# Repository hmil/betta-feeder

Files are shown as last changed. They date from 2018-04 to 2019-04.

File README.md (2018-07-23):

DIY IoT Feeder for my Betta Fish
================================

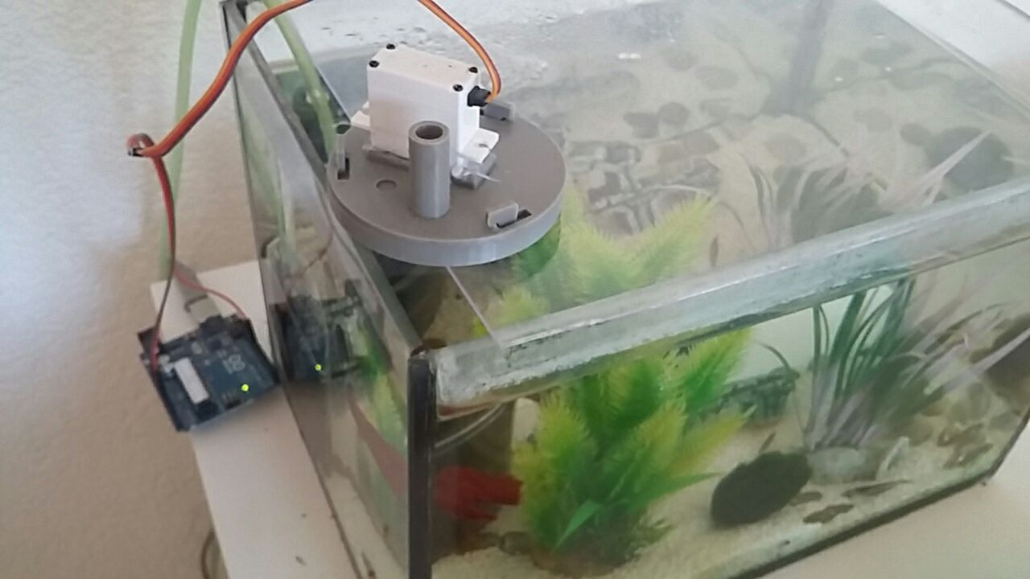
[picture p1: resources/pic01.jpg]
Feeder picture

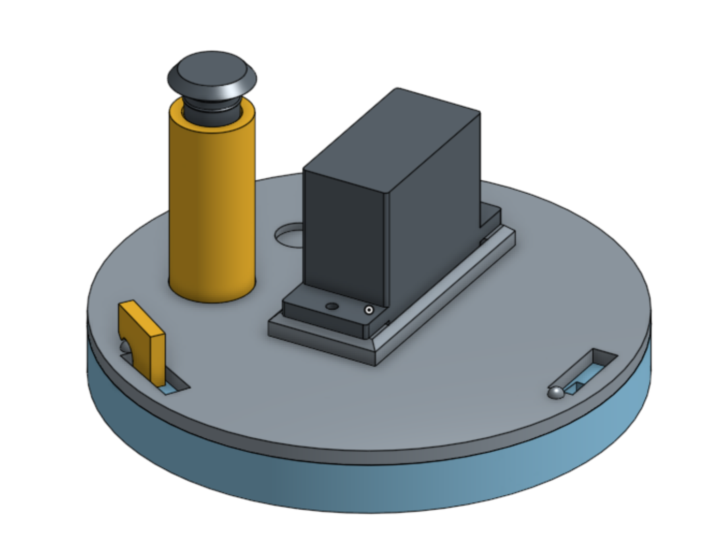
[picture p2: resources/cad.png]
CAD model rendering

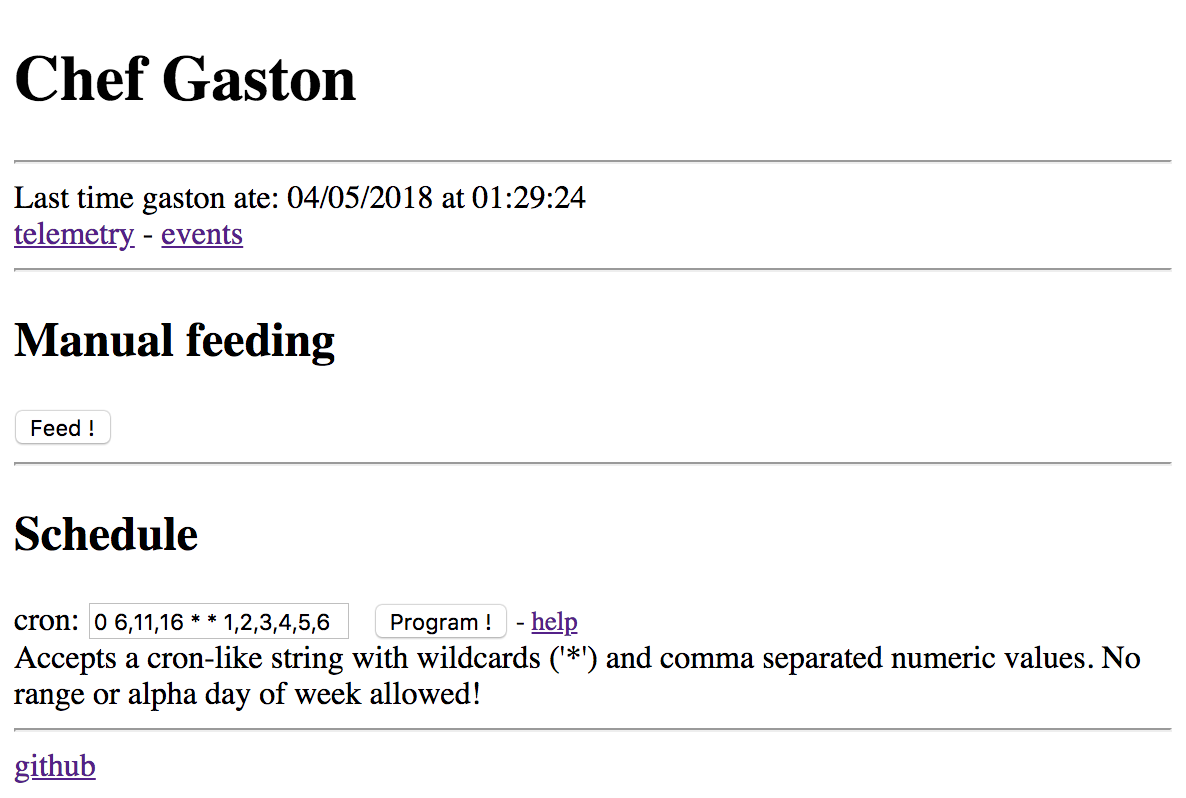
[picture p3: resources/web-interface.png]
web control interface


## Features

- precise quantities, food is delivered in predefined increments
- Large autonomy: The system works as long as there is food left in the reservoir.
- Robust design with only one moving part.

## What you need

- An arduino board OR a NodeMCU / ESP-12 or any esp8266-based board supported by NodeMCU
- A servomotor
- An AC adapter for the arduino / MCU
- A 3d printer

## Setup

Print and assemble all parts according to the cad model. Make sure to leverage the base plate of your printer to get smooth surfaces for the inside of the case and the base of the rotor (this will prevent food from getting caught between the rotor and the case).
Mount the servomotor on top and connect it to the arduino's VCC (red wire), Gnd (black wire) and pin 9 (remaining wire). I found that the capacitors on the board are sufficient to operate the servo without loss of power. If you do lose power when the servo moves, connect the servo's red and black wire through a breadboard and put one or two capacitors of more than 100uF in between.

## How it works

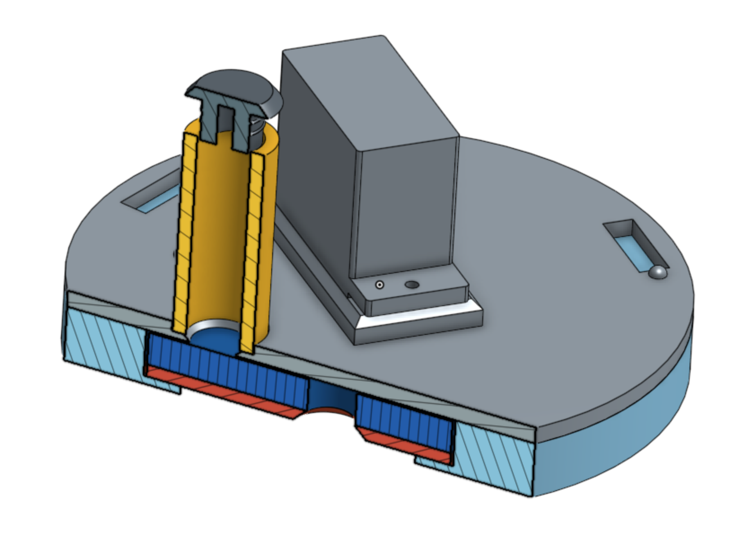
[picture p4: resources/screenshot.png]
Cut view


A hole on a rotating disk alternatively aligns with a food reservoir on top and a dispensing hole at the bottom. The disk is actionned by a servomotor at scheduled times.

## Hardware

The CAD is [hosted at onshape](https://cad.onshape.com/documents/9ce24f0eb68b5dfcb29f30d2). You will probably need to modify it so that it fits your specific servo.

Be sure to print the surfaces that will be in contact with the rotor facing the bottom. This way you'll get the smoothest possible surfaces and prevent food from getting stuck into the mechanism.

Ready-to-print STL files are available under `hardware/`. Tested on a prusa i3 mk2; It took a little bit of grinding to get them all to fit together.

## Software

### Arduino

There is an arduino sketch providing basic functionality. It is a prototype and has major flaws:
- Programming the schedule requires to change the software code and flash the arduino with the new program.
- The schedule is relative to the boot time of the arduino. In the event of an AC outage, there is a risk for feeding too much or too little.

### NodeMCU

A NodeMCU project is available as well. It is safer and has more features than the arduino code, but is a little more complex to use.

Connect the servomotor to GPIO 12. Be careful that the board runs at 3.3v whereas a servo usually runs at 5v (You don't need a logic converter for the control signal... just beware not to connect the board's 3.3v to the servo's VCC). Make a copy of the `.example` files without the `.example` extension and replace the variables according to your environment.

The NodeMCU software must be configured to talk to an MQTT broker. A companion server (located in `/server`) provides a user interface and connects to the same broker to collect data and send commands to the device. Run the server with Node.JS and the proper environment variables (MQTT_HOST, MQTT_PORT, MQTT_USER, MQTT_PASSWORD).

The server lets you manually trigger the feeder and allows you to program the schedule using a cron-like syntax. It also lets you see historical data of the device.

Contrary to the Arduino sketch, the NodeMCU solution is more reliable as it uses NTP to keep track of wall clock time. There is no risk of over-delivery and little risk of missed deliveries.

## Known issues

- There is not enough play between the rotor and the carter and it requires quite a bit of grinding to get it to slide well.
- The top part is designed based on an unusual servomotor format. (I got a larger servo to fit using hot glue though).
- The reservoir is too narrow and is a real pain to refill.

**If you fix any of these issues, make sure to contribute your changes back!**

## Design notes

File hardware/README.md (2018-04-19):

This folder contains STL files exported from [this onshape project](https://cad.onshape.com/documents/9ce24f0eb68b5dfcb29f30d2).

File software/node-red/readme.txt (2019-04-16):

This is a companion application which talks to the nodemcu-based software over MQTT.

It is implemented with node-red.

Deploy a node-red instance and import flow.json into it. You'll need to configure the paths of 
the file storage and the sqlite database, as well as the credentials to connect to your MQTT server.

The flow uses the following modules:
- https://flows.nodered.org/node/node-red-dashboard
- https://flows.nodered.org/node/node-red-node-sqlite

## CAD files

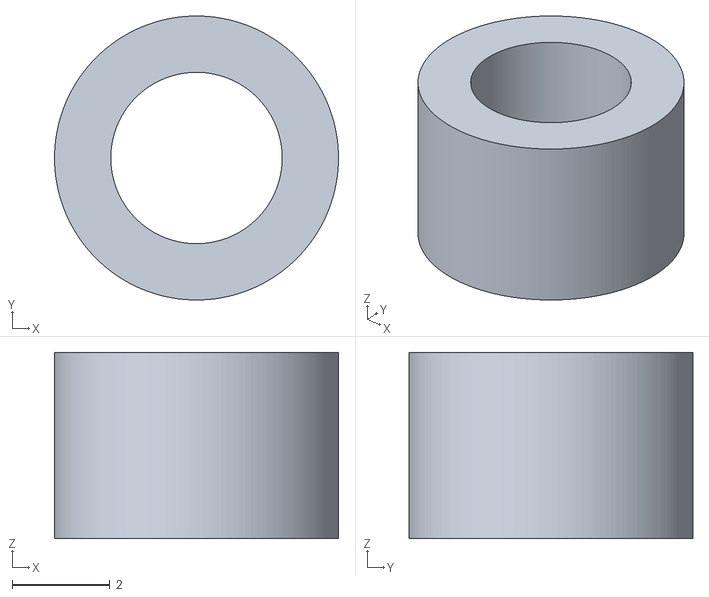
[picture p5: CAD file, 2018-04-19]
hardware/reducer insert 2.stl
5.80 x 5.80 x 3.80

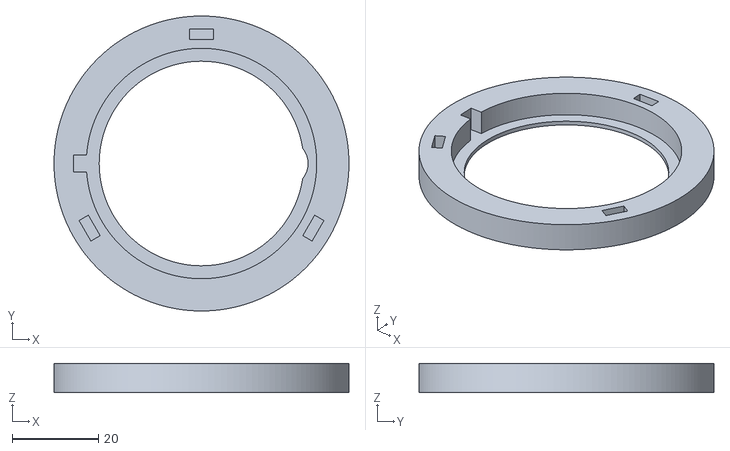
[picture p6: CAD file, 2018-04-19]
hardware/carter.stl
68.5 x 68.5 x 6.75

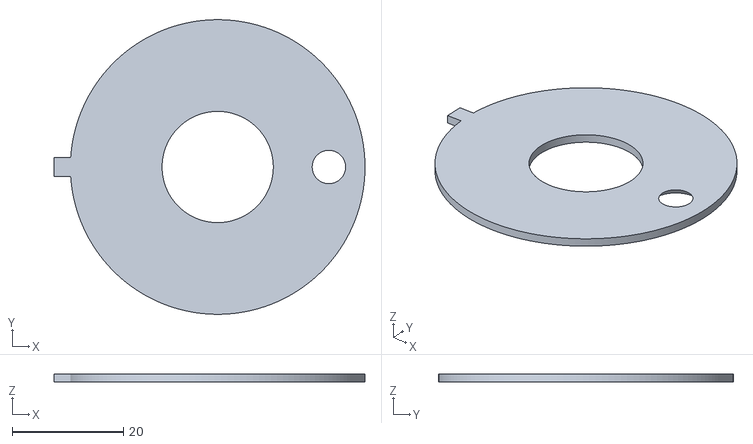
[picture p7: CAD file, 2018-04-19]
hardware/base plate.stl
55.9 x 53.0 x 1.50

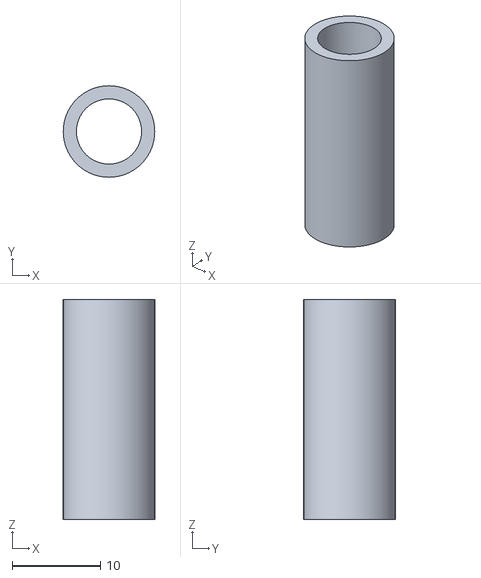
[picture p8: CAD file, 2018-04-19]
hardware/reservoir.stl
10.4 x 10.4 x 25.0

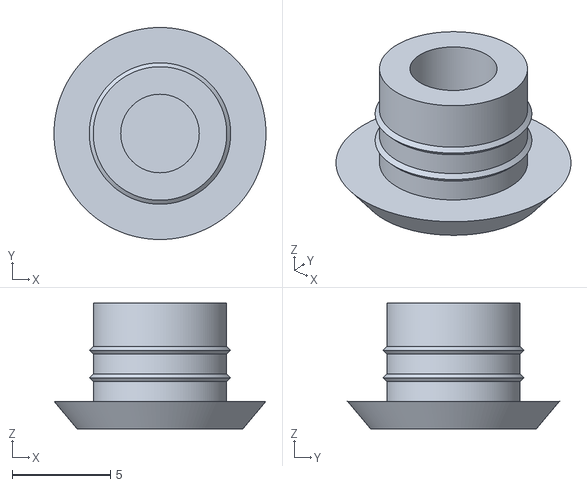
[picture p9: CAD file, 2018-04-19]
hardware/reservoir cap.stl
10.8 x 10.8 x 6.40

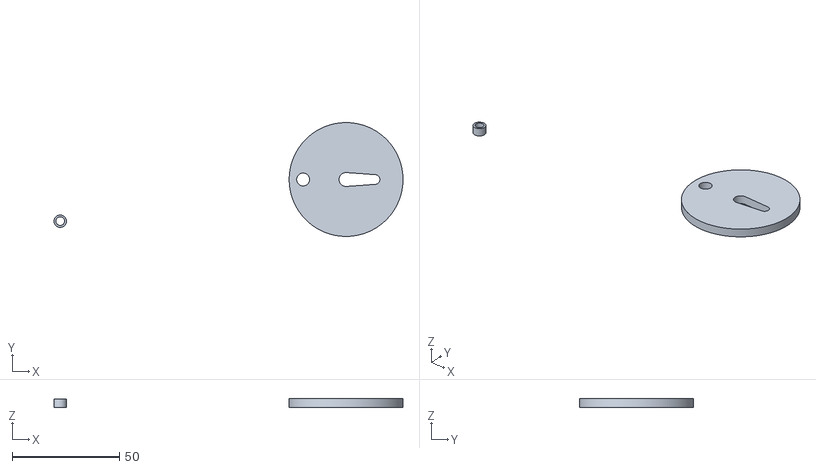
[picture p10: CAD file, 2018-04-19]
hardware/reducer insert 1.stl
162.5 x 53.0 x 4.00

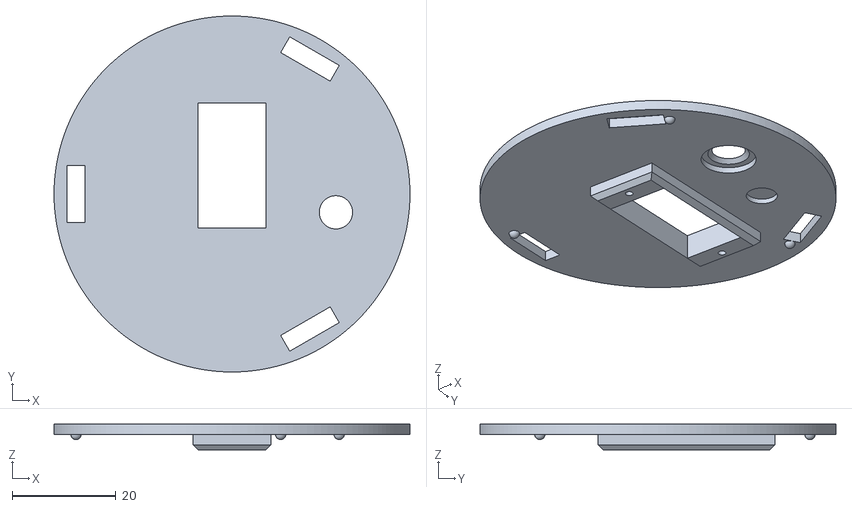
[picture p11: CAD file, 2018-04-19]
hardware/top.stl
68.5 x 68.5 x 5.00

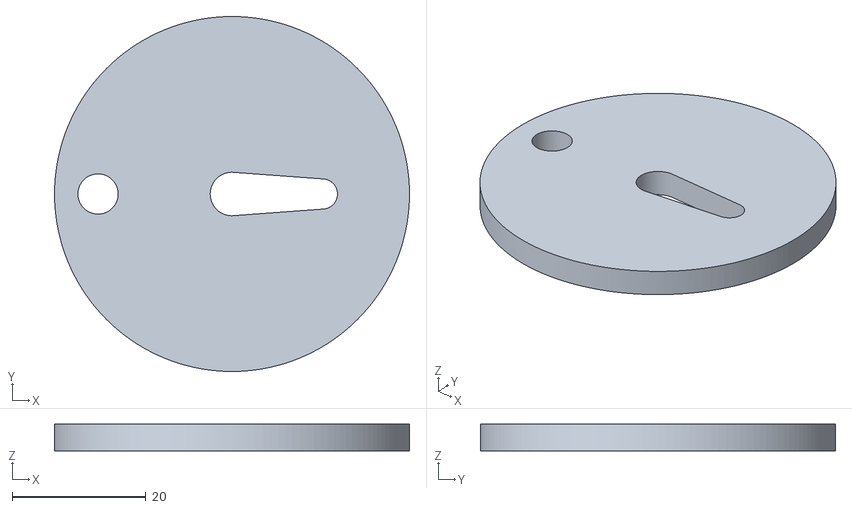
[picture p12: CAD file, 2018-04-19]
hardware/rotor.stl
53.0 x 53.0 x 4.00

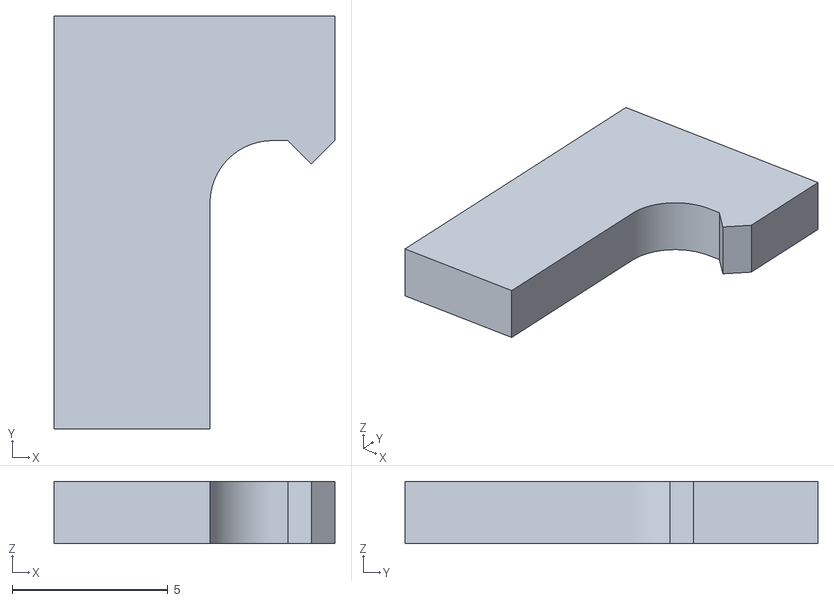
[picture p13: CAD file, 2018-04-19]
hardware/lock key (x3).stl
9.00 x 13.2 x 2.00

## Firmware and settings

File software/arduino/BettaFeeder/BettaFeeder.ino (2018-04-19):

#include "TimeLib.h"
#include <Servo.h>

Servo myservo;

int state = 0;

// Servo position where the rotor hole is aligned with the bottom hole
int pos_release = 83;

// Servo position where the rotor hole is aligned with the top hole
int pos_take = 35;

// Number of doses given each time the feeder fires
int n_portions = 1;


void setup() {
  Serial.begin(9600);
  pinMode(13, OUTPUT);
  myservo.attach(9);
  myservo.write(pos_take);
}

void turnDatShit() {
  myservo.write(pos_take);
  delay(1000);
  myservo.write(pos_release);
  delay(1000);
}

// You may want to change this to your custom schedule.
// The time starts at 0 when you power the arduino on.
int shouldDistribute() {
  return second() == 0 && minute() == 10 && (
    hour() == 0 ||
    hour() == 14
  );
}

void printDigits(int digits){
  // utility function for digital clock display: prints preceding colon and leading 0
  Serial.print(":");
  if(digits < 10)
    Serial.print('0');
  Serial.print(digits);
}

void printTime() {  
  // digital clock display of the time
  Serial.print(hour());
  printDigits(minute());
  printDigits(second());
  Serial.print(" ");
  Serial.print(day());
  Serial.print(" ");
  Serial.print(month());
  Serial.print(" ");
  Serial.print(year()); 
  Serial.println(); 
}

void loop(){
  if (shouldDistribute()) {
    for (int i = 0 ; i < n_portions ; i++) {
      turnDatShit();
    }
    delay(1001); // Makes sure we don't double spend
  }
  if (timeStatus() == timeSet) {
    digitalWrite(13, HIGH); // LED on if synced
  } else {
    digitalWrite(13, LOW);  // LED off if needs refresh
  }
  delay(500);
  printTime();
}

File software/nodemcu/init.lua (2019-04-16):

-- What we found so far:
-- enduser_setup handles all wifi stuff by itself
-- servos are controlled by pulse length
-- with nodemcu's pwm module this means create a pwm with freq 50Hz and vary duty between 30 and 125

dofile('env.lua')

local servoPosTake = 75
local servoPosRelease = 100
local servoPosNeutral = 120

CONFIG_FILE="config.json"
SERVO_GPIO=6

config = {}
config["cron"] = "0 10 * * *"
config["doses"] = 1

pwm.setup(SERVO_GPIO, 50, servoPosNeutral)
pwm.start(SERVO_GPIO)

feedcron = nil

enduser_setup.start()

sendStatus = function()
    if client ~= nil then
        client:publish("/gaston/status", '{"config":' .. sjson.encode(config) .. '}', 0, 0, function(client) print("sent") end)
    end
end

sendEvent = function(type)
    if client ~= nil then
        sec = rtctime.get()
        client:publish("/gaston/events", '{"event":"' .. type .. '","epoch":' .. sec .. '}', 0, 0, function(client) print("sent") end)
    end
end

updatecron = function()
    if feedcron == nil then
        local tryInit = pcall(function()
                feedcron = cron.schedule(config.cron, function()
                    dispense()
                    sendStatus()
                end)
            end)
        if tryInit == false then
            print('config is corrupt! Erasing config...')
            file.remove(CONFIG_FILE)
            node.restart()
        end
    else
        feedcron:unschedule()
        feedcron:schedule(config.cron)
    end
end

setConfig = function(cfg)
    if cfg.cron ~= nil then
        config.cron = cfg.cron
    end
    if cfg.doses ~= nil then
        config.doses = cfg.doses
    end
end

loadConfig = function()
    if file.open(CONFIG_FILE, "r") then
        local data = file.read()
        file.close()
        setConfig(sjson.decode(data))
    end
end

writeConfig = function()
    if file.open(CONFIG_FILE, "w+") then
        file.write(sjson.encode(config))
        file.close()
    end
end

dispenseOne = function(cb)
    pwm.setduty(SERVO_GPIO, servoPosTake)
    tmr.create():alarm(1000, tmr.ALARM_SINGLE, function()
        pwm.setduty(SERVO_GPIO, servoPosRelease)
        tmr.create():alarm(1000, tmr.ALARM_SINGLE, function()
            cb()
        end)
    end)
end

dispense = function()
    print('Dispensing...')
    sendEvent('dispense')
    
    local remainingDoses = config.doses
    dispenseRec = function()
        dispenseOne(function()
            remainingDoses = remainingDoses - 1
            if remainingDoses > 0 then
                dispenseRec()
            else
                pwm.setduty(SERVO_GPIO, servoPosNeutral)
                print('Done dispensing.')
            end
        end)
    end
    dispenseRec()
end

connectTries = 0
connect = function()
    connectTries = connectTries + 1
    m:connect(MQTT_HOST, MQTT_PORT, MQTT_SECURE, function(cl)
        print("mqtt connected")
        client = cl
        client:subscribe("/gaston/commands", 0, function(client) print("subscribe success") end)
        sendEvent('connect')
        sendStatus()
    end,
    function(client, reason)
        print('Mqtt failed, reason: ' .. reason)
        tmr.create():alarm(10 * 1000, tmr.ALARM_SINGLE, connect)
    end)
end

initMqtt = function()
    m = mqtt.Client("gaston0", 60, MQTT_USER, MQTT_PASSWORD)

    -- setup Last Will and Testament
    -- Broker will publish a message with qos = 0, retain = 0, data = "offline" 
    -- to topic "/lwt" if client don't send keepalive packet
    m:lwt("/lwt", "offline", 0, 0)

    m:on("offline", function(client)
        print ("offline")
        tmr.create():alarm(10 * 1000, tmr.ALARM_SINGLE, connect)
    end)

    -- on publish message receive event
    m:on("message", function(client, topic, data) 
        print(topic .. ":") 
        if data ~= nil then
            print(data)
        end

        decoded = sjson.decode(data)

        if decoded.dispense == true then
            dispense()
        end

        if decoded.config ~= nil then
            setConfig(decoded.config)
            writeConfig()
            updatecron()
        end

        sendStatus()
    end)
end

main = function()
    local hasTime = false
    local hasWifi = false

    loadConfig()
    initMqtt()

    local onComponentInit = function()
        if hasTime == true and hasWifi == true then
            updatecron()
            connect()
        end
    end

    -- Init clock with network time
    sntp.sync(nil, function()
        print('Success getting time')
        hasTime = true
        onComponentInit()
    end, function(e)
        print('Error getting time: ' .. e)
    end, true)
    
    -- Init wifi listener
    wifi.eventmon.register(wifi.eventmon.STA_GOT_IP, function(T)
        print("\n\tSTA - GOT IP".."\n\tStation IP: "..T.IP.."\n\tSubnet mask: "..
        T.netmask.."\n\tGateway IP: "..T.gateway)
        hasWifi = true
        onComponentInit()
    end)
end

main()

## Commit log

2018-05-07 fix buggy mqtt connection
    [init.lua]
2019-04-16 Update software stack
    [fritzing.fzz]
